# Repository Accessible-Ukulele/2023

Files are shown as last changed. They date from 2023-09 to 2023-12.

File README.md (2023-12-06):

# Accessible Ukulele
A repository for project code, reports, and more. NOT FINAL   
Created by:  
Kaleb Keller,   
Ryan Loar,  
Kameron Lund,  
and Dominic Pedavoli  

The Accessible Ukulele strives to eliminate the fine motor skills required to play the ukulele, to make playing music more accessible for amputees or those with fine motor control disabilities. The device allows the user to play chords at the press of a button using six precisely placed solenoids, that press down the strings of the ukulele.

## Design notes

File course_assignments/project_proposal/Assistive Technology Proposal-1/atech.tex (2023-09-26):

% This is the atech.tex This is where your writ ting will actually occur. In addition you will use this to display pictures, make tables, and format your paper. You should ONLY change things in this document.

% Calls up multiple packages that tell the computer ow you want to format the text and what neat tools you want to include so that you can use.

\documentclass[12pt]{article}
\usepackage{fancyhdr}
\usepackage{lettrine}
\usepackage[english]{babel}
\usepackage{graphicx}
\usepackage{gensymb}
\usepackage{listings}
\usepackage{multicol}
\usepackage{amsmath}
\usepackage{fancyvrb}
\usepackage{verbatim}
\usepackage{float}
\usepackage{multirow}
\usepackage{mathdesign}
\usepackage{txfonts}
\usepackage{mathrsfs}
\usepackage[justification=centering]{caption}
\usepackage{subcaption}
\usepackage{mdsymbol}
\usepackage{wrapfig}
\makeatletter
\def\mycatheader#1{\multicolumn{\tabu@nbcols}{c}{#1}}
\makeatother
\pagestyle{fancy}
\usepackage{mcode}
\providecommand{\e}[1]{\ensuremath{\times 10^{#1}}}

% Your class and semester here!
\lfoot{ECEN 1400}
\rfoot{Fall 2023}
 
% Defines that all Images are in the folder "images/" so that we don't have to type it repeatedly
\graphicspath{ {images/} }

% Catchy Name of your Project followed by 
\title{Atech Proposal: your project name}
%  followed by 
% Names {First Last} in Alphabetical Order by Last Name Go in Here 
\author{
  Name One \footnote{email1},
  Name Two \footnote{email2},
  Name Three \footnote{email3},
  Name Four \footnote{email4}\\
    {\normalsize 
   Lecture Section 100, ECEN 1400}\\
 }

% Tells the Document you are ready to start typing
\begin{document}

% Explains to the document to put in the Title, Names  onto a cover page
\maketitle

% This should be an ~200 word summary of the proposal
\begin{abstract}
An abstract is a block of text at the beginning of the paper that is usually around 200 words long. It is a conclusive statement of your entire proposal. 
\end{abstract}

% This ends the Title and Abstract page and lets you move on to the real report!

%This makes a new page 
\newpage

% This will make a Table of contents that Updates Automatically!
\tableofcontents

% This ensures it stays on its own page -- please be sure to do a new page before each new section (not subsection)
\newpage

% Begin a New Overarching topic
\section{Inspiration}
\newpage

\section{Project Scope}
The \textbf{scope} of the project will help you define the effort required and your plan to meet the specifications. This will help you figure out if the project is \textit{right sized} for the time you have. This judgement will depend on your skills - one size does not fit all.
% Begin a Sub-Topic
\subsection{Goals}
The goal and mission of your group should be in here. In addition pertinent information regarding your client (if you have one) will be very important. You should be explaining who they are before you explain what they need you to do! Be \textbf{very} descriptive.  What are your goals for the project? What is important for you to get out of it? These could be learning goals or specific performance milestones. (not the dates of PDR, CDR etc but what will be done) 

\subsection{Team Assignments}
Each should include a short description of what each person will do, sufficient to judge the effort and complexity of their task. What background, if any, does the team member bring that is relevant to achieving their goal? Everyone must do some technical design work – not just paperwork. Though certain students may have a larger or smaller technical role.

\subsection{Plans to Achieve Goal}
Depending on the project, describe:
\begin{itemize}

\item What will you design and build vs. what will you buy? (Buying pieces to help the design work is acceptable for this project)

\item What resources are available (people, existing designs) that increase your capability?

\item What will your project NOT do?

\end{itemize}

\newpage

\section{Specifications}

To the best of your ability now, list quantifiable performance specifications. Be as complete as you can. It is much more important that you think of the entry, (e.g. “Battery Life in Hours”) than you know the value.

% have text introducing the table

\begin{itemize}

    \item Start with categories, then work on individual entries.

    \item Present this in the form of a table. For each spec, list minimum, nominal and maximum values if known, \textit{as appropriate}. Include a column for units.

\end{itemize}
%Google "latex table format" 

\newpage

\section{Design Iteration}

% Sub-Topic 1
\subsection{Design Elements}
% each as appropriate for your project
This should be a full length description of your initial ideas/parts with beautiful pictures to match. I have elected to leave in a groups photo of their project to show how to insert a graphic below!

% This is how you insert a graphic. This is very, very important. Have this ready to go at all points. Always caption and use a label with your figure. Always reference the figure before you insert it.

% How to call a figure that has been labeled so you don't have to keep track of numbers.

Figure \ref{fig:frame} shows a rendering of our project frame including (be descriptive) a clear object in the front and the mounting system.

\begin{figure}[H]
% Puts your image in the center of the page, multiple other justifications are able to be done
\centering
    % Actually include the graphic
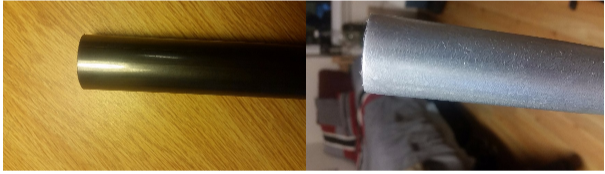
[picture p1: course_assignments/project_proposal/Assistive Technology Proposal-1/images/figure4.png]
    
    % CAPTIONS ARE VERY IMPORTANT NO FLOATING PICTURES
    \caption{Comparison of galvanized metal (right) to weldable steel (left)}
    % This is how we can tell the code what picture we are referencing.
    \label{fig:frame}
\end{figure}

\begin{itemize}
\item Block Diagram Electrical
\item Software Flow Chart
\item Block Diagram Mechanical
\item Sketch of package / external design - hand drawings are acceptable (if done in dark ink and readable - but preliminary CAD is encouraged. This should include how major components (in size or importance) are expected to “fit” in the project.
\item \textbf{Estimated}  bill of materials (BOM) as a \textbf{table} including cost for critical and expensive items. Total the cost. 
\end{itemize}

% Please use numbers/equations

In case you were wondering, you can use equations! See Equation \ref{eq:Strain}. This one happens to represent strain on a bar.

% This is how to use an equation, a mathematical Symbol, Fractions, and underscores
\begin{equation}
    \sigma = \frac{F}{A_{0}}
    \label{eq:Strain}
\end{equation}

% New Topic
\newpage
\section{Risk Mitigations}
\begin{itemize}
    \item List possible (significant) risks to success and briefly describe your plan to overcome these. Suggest minimal performance and alternative approaches or alternative goals to be successful. (think safety, supply chain issues, illness of team member, etc..)
    \item Think creatively about this.
\end{itemize}

% Another Figure example
In Figure \ref{fig:cage} you can see an old picture of the cage. 
\begin{figure}[H]
\centering
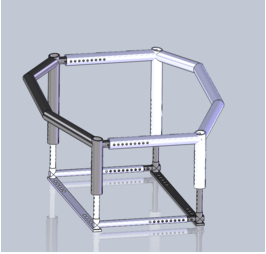
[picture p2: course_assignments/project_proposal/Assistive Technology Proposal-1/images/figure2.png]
    
    \caption{Original 3D model of the cage}
    \label{fig:cage}
\end{figure}

\newpage
\section{Timeline}
% New Sub-Topic
Look at the semester schedule including assignment milestones. Create a list of performance milestones by date. (what will get done by when) Include deliverables on sub-tasks such as electronics or software.  Use a \textbf{Gantt Chart} made using excel or something like excel.  Avoid using commercial packages or templates to create the chart, especially those that are complicated.

\newpage
\section{Tools}
Tools that will be used (laser cutter, 3D printer, sewing machines, milling machine). 
Put in any other tools you might have used!

\newpage
\section{Anything else you can think of that is helpful}

\newpage
\section{Closing Statements}
A strong argument for the success of this project
 
\newpage

% Anything Pertinent but without a real place, or if it doesn't fit in your discussion section.
\section{Appendix}

% Close and render the paper to a PDF format
\end{document}

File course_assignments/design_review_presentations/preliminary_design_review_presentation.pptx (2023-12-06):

## The Accessible Ukulele The Joule Jugglers

Dominic Pedavoli
Kaleb Keller
Kameron Lund
Ryan Loar

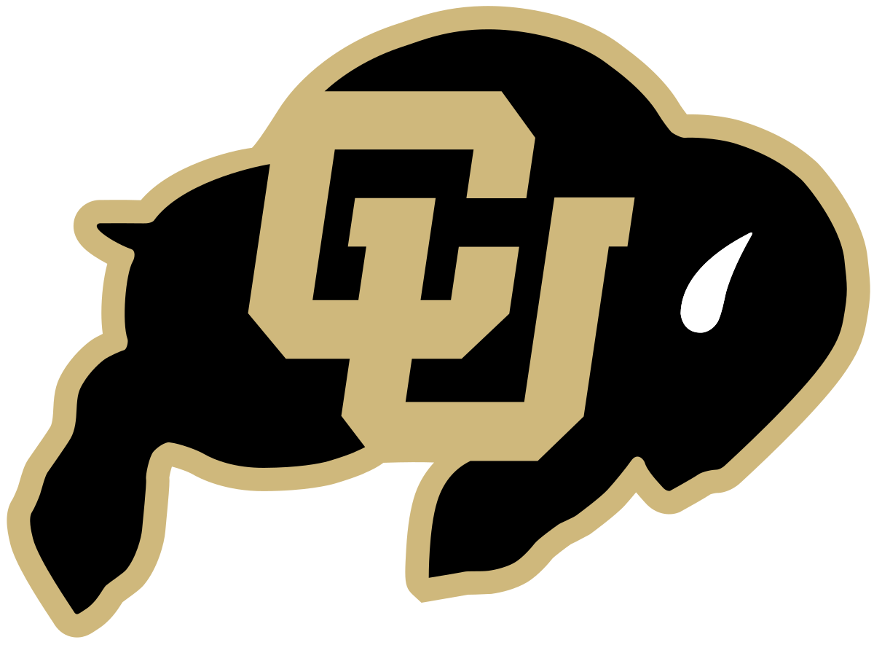
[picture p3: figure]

## For The Love of Music

- Form of expression
- Relaxing
- Outlet to relieve stress
- Not always accessible to everyone

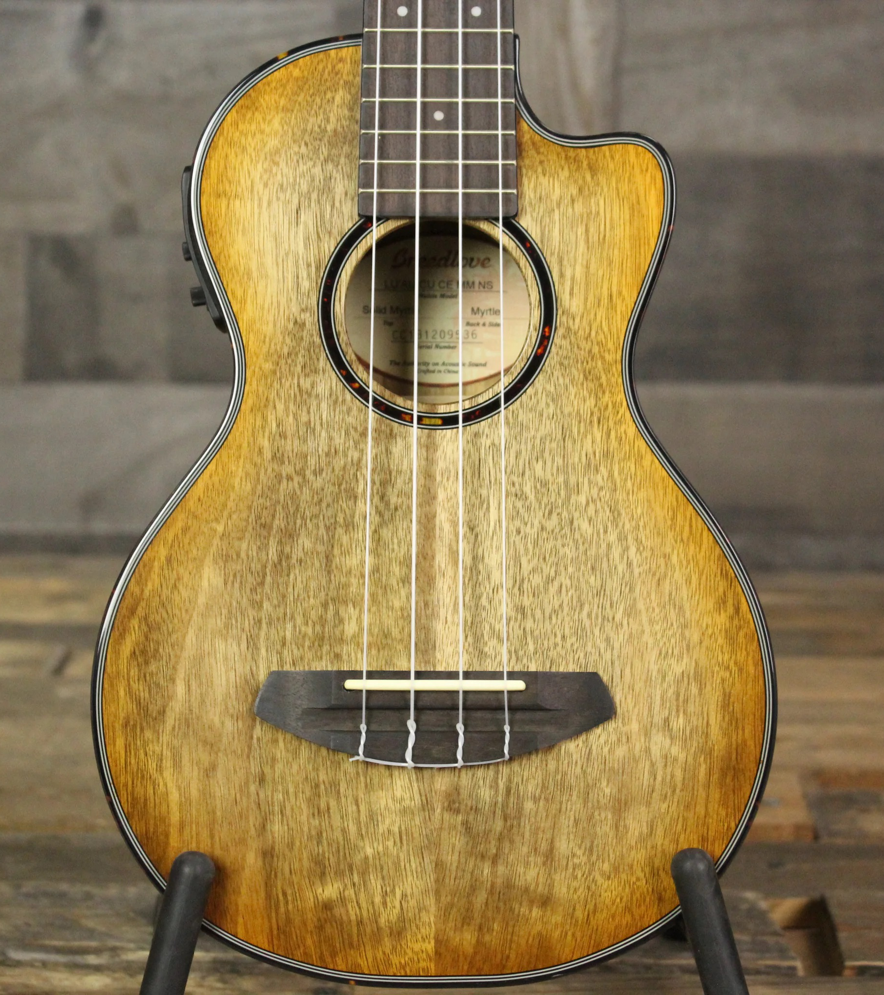
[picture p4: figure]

## Problem Statement

The ability to play music is not accessible to everyone. Those with a fine motor control disability can find it difficult to play music as an outlet of expression. This problem can begin to be solved by simplifying the way instruments can be played.

## Outline

Our Target Market

Design Inspiration

Expected Timeline

Cost of Materials

Original Circuit Diagrams

Plans for Testing

Goals

Definition of Success

## Client Introduction – Our Target Market

Intended for those who lack fine motor control in hands
Not trying to replace the ukulele
Simplifying the way, it's played and giving options to those in need

## Design Inspiration

- Guitar Hero (Top Right)
- Beginner Chord (Top Left)
- EZ Fret (Bottom Left)
- Our Initial Design Idea (Bottom Left)

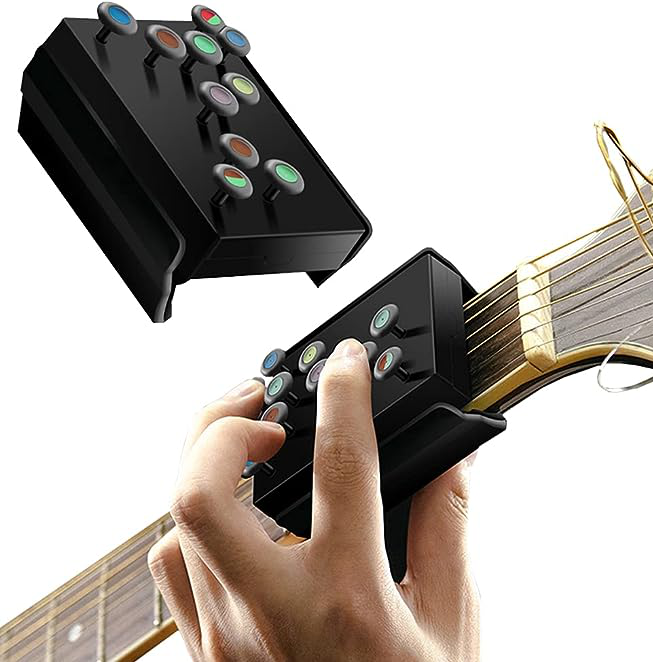
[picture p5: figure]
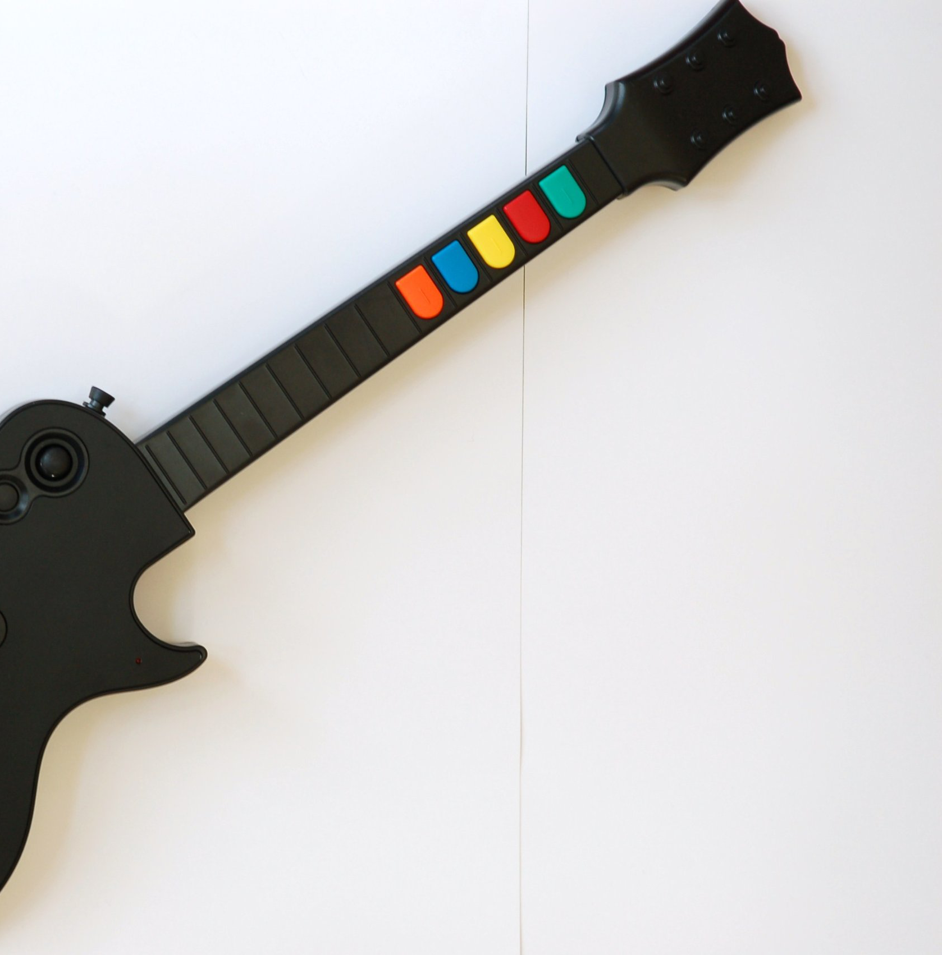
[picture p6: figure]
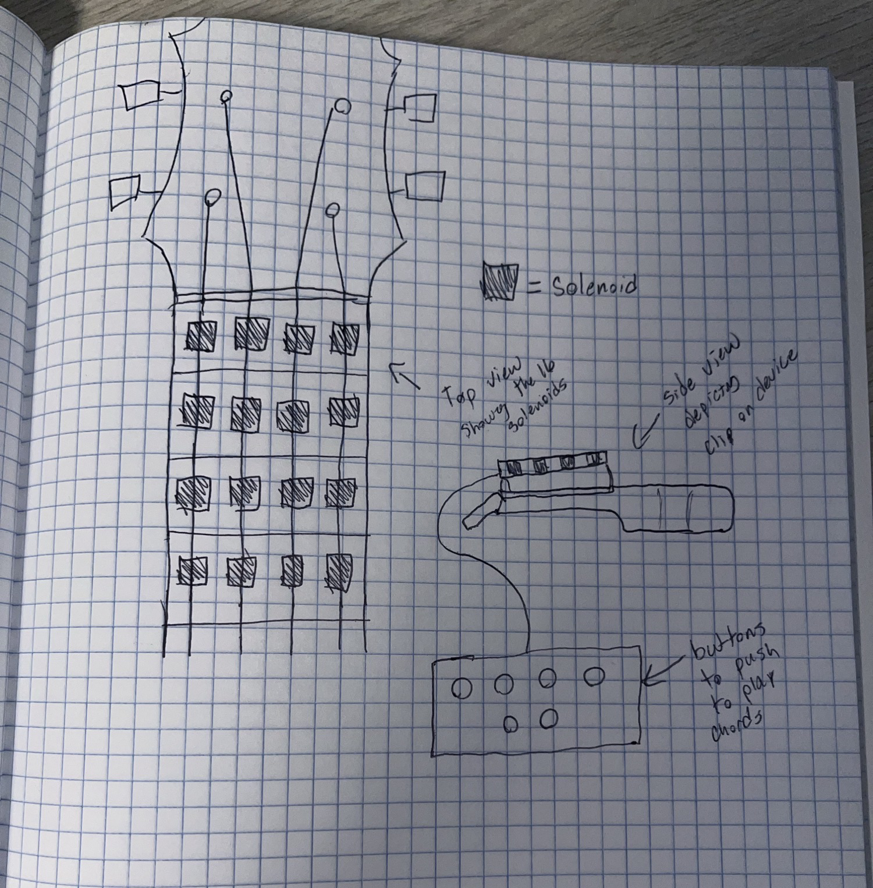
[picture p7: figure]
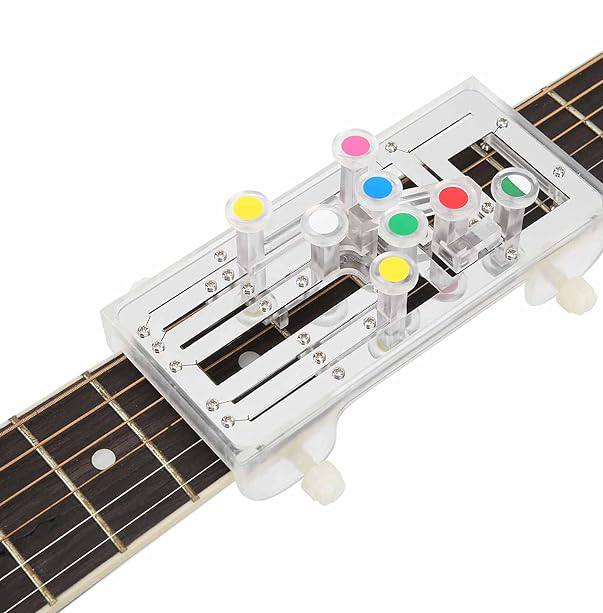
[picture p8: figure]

## Timeline/Task Assignments

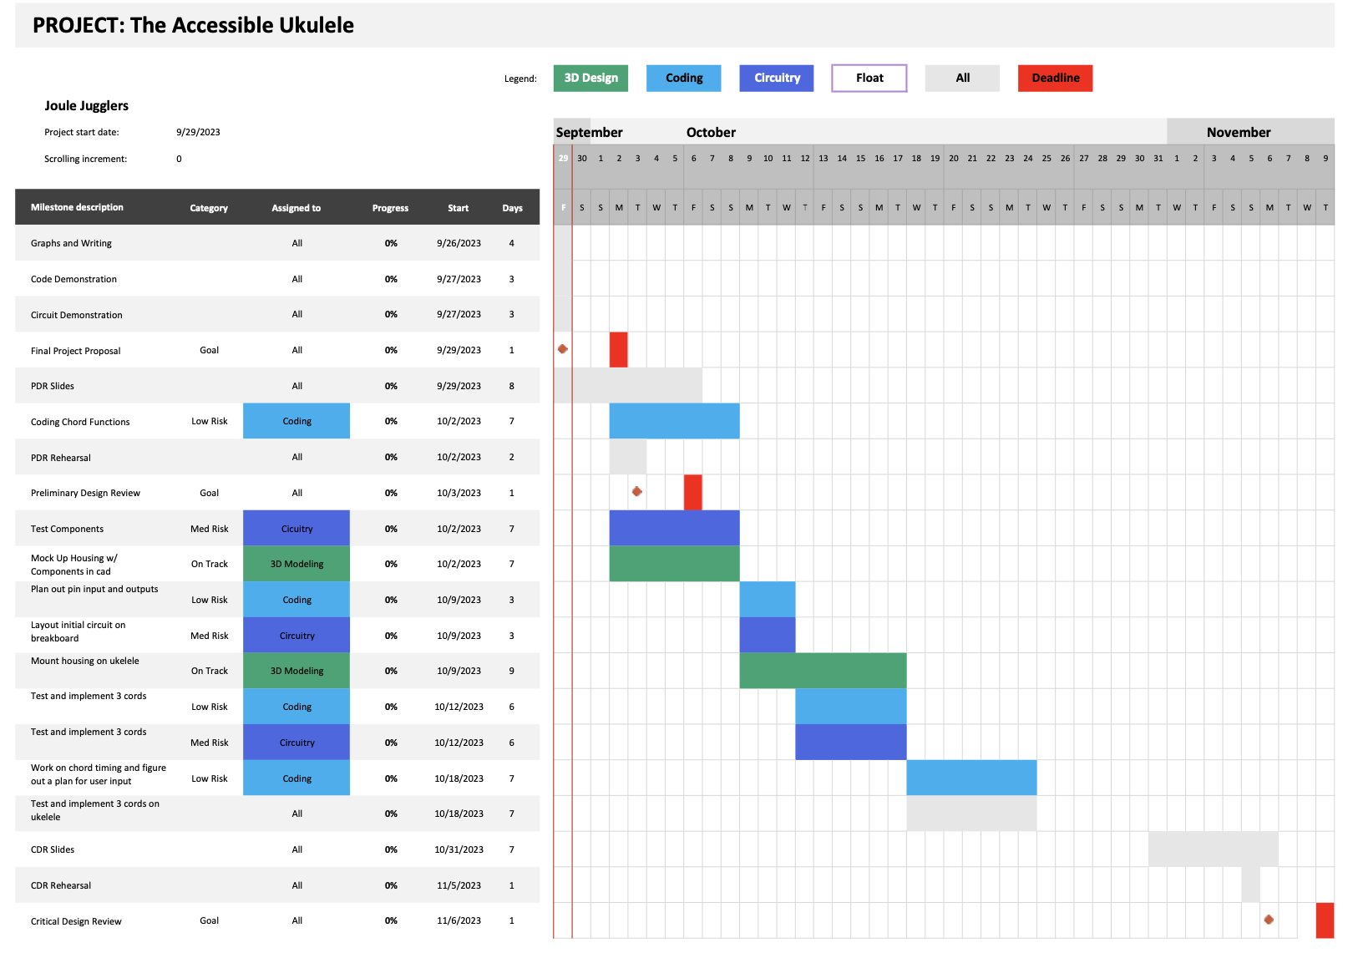
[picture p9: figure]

Gantt chart of our timeline

- Kameron - coding
- Dominic - circuitry
- Kaleb - 3D design
- Ryan - float
- Organizing time based on musical milestone
- Design as individuals and come back together to test and iterate as a group

## Budget/Bill of Materials

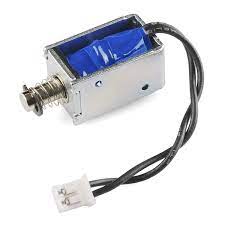
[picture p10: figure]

Solenoids (x16):
Buttons (x4):
Arduino Mega (Elegoo) (x1):
Transistors (x16)
Miscellaneous:
Total:
Budget Maximum:
Margin:

$88.00
$51.80
$21.00
$0.00
$15.00
$175.80
$300.00
$124.20

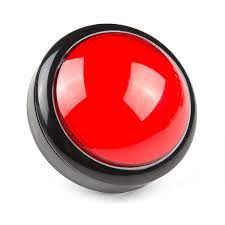
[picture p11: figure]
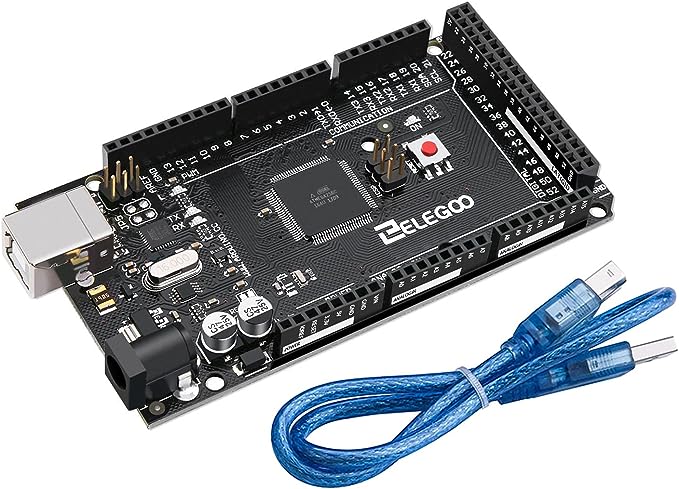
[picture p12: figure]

## Plans for Testing

- Test materials immediately after their arrival
- Test code consistently and thoroughly as we develop it
- Test circuits on breadboard before soldering wires
- Print housing and parts early
- Test compilation of parts
- Regularly test all tasks together once completed

## Circuit Diagram

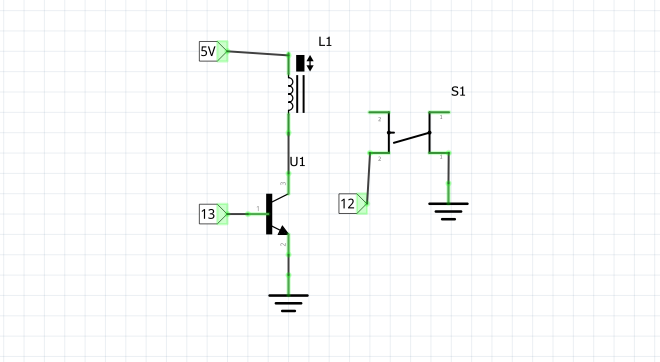
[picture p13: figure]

*Diagram for 1 of 16 solenoids

## Definition of Success

With this project we will…
- Respect and preserve the individual creativity of the musician
- Fundamentally change the range of physical motion required for musical expression
- Respect the instrument for its complexity (it's not a toy)
- Design in a way that maximizes accessibility while minimizing triviality
- Separate music as an art form from physical ability

## Conclusion

- Ease the process of playing stringed instruments
- Keep outcomes (sound) the same
- Regularly test (physical and digital)
- Explore new input avenues (buttons vs motion control vs app)
- Explore coding solutions to physical problems (manage button switching)

## Any Questions?

## How Do Solenoids Work?

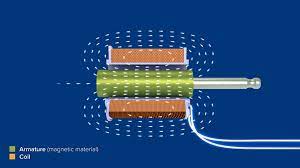
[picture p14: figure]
A diagram of a device
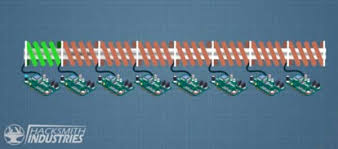
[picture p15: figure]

## What If The Solenoids Don't Work?

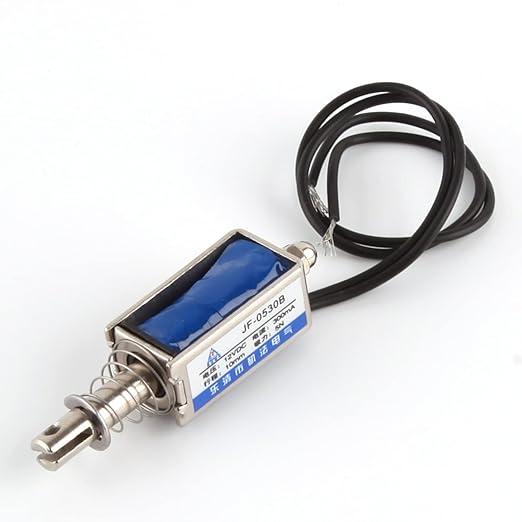
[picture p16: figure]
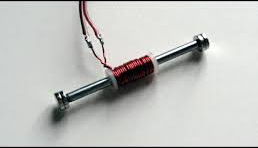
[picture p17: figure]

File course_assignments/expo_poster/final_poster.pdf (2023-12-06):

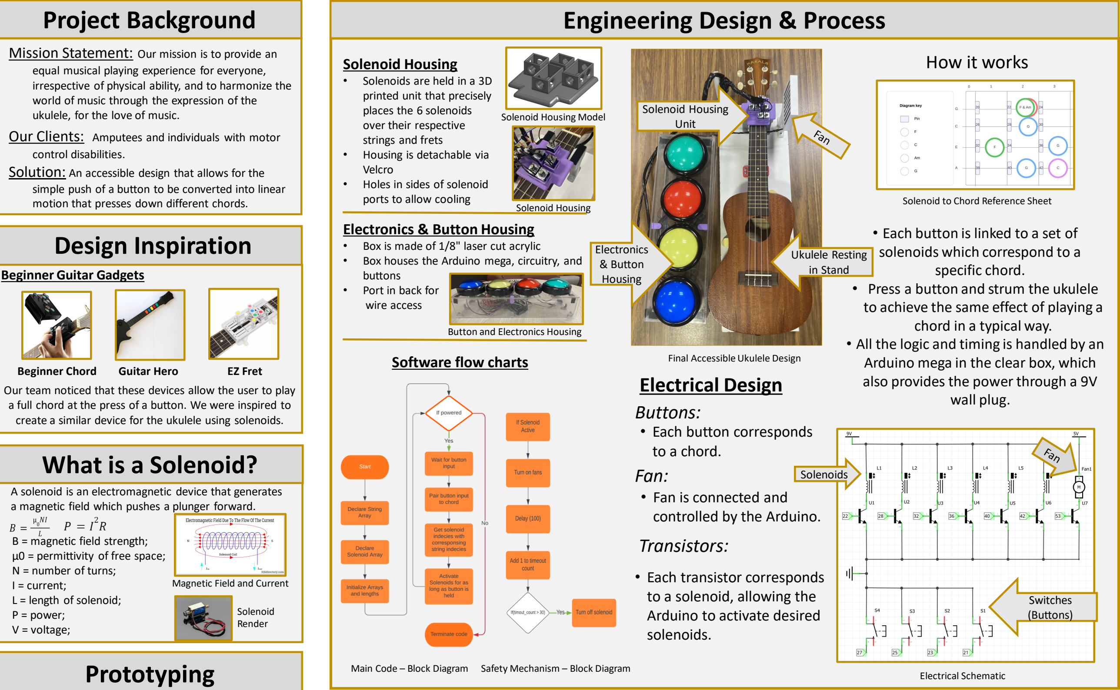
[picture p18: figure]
ukulele, for the love of music.; control disabilities.; Project Background; Prototyping; Engineering Design & Process; Beginner Guitar Gadgets; Software flow charts; • Each button corresponds to a chord.; Buttons:; Electrical Schematic; What is a Solenoid?; Main Code – Block Diagram; Safety Mechanism – Block Diagram; Beginner Chord; Solenoid Housing; • Solenoids are held in a 3D printed unit that precisely places the 6 solenoids over their respective strings and frets • Housing is detachable via Velcro • Holes in sides of solenoid ports to allow cooling; How it works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

Mission Statement: Our mission is to provide an equal musical playing experience for everyone, irrespective of physical ability, and to harmonize the world of music through the expression of the

Our Clients: Amputees and individuals with motor

Solution: An accessible design that allows for the simple push of a button to be converted into linear motion that presses down different chords.

A solenoid is an electromagnetic device that generates a magnetic field which pushes a plunger forward.

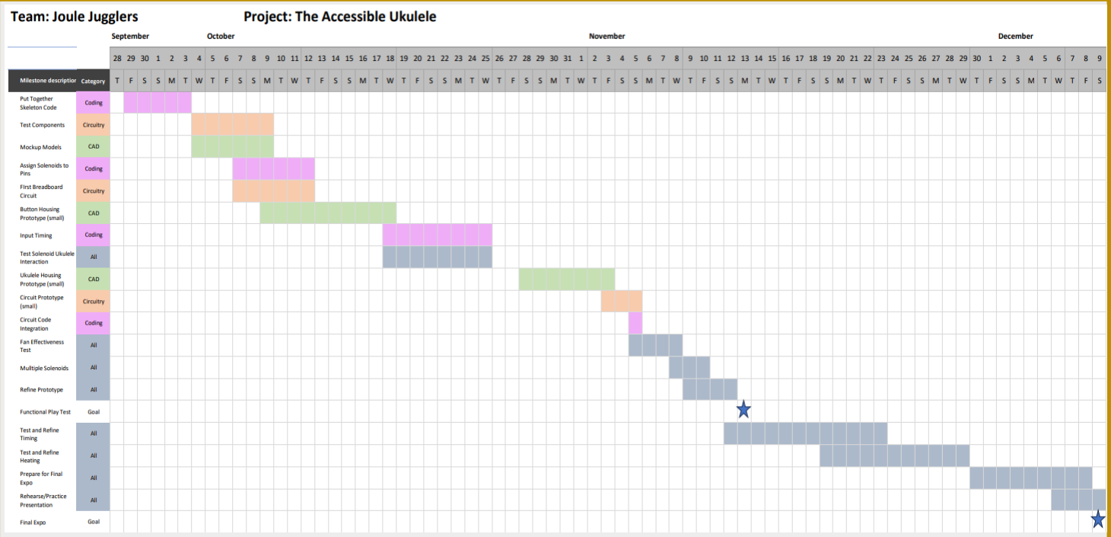
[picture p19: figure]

### - Potential exposure to live wires (as few as possible

with our constraints).

### - Solenoids are prone to producing a large amount of

heat.

### - Fan engages when the solenoid(s) are active, ensuring

that the solenoid never reaches above 100° F.

### - Fans use convection cooling to push air past the

solenoid housing, dispersing the heat.

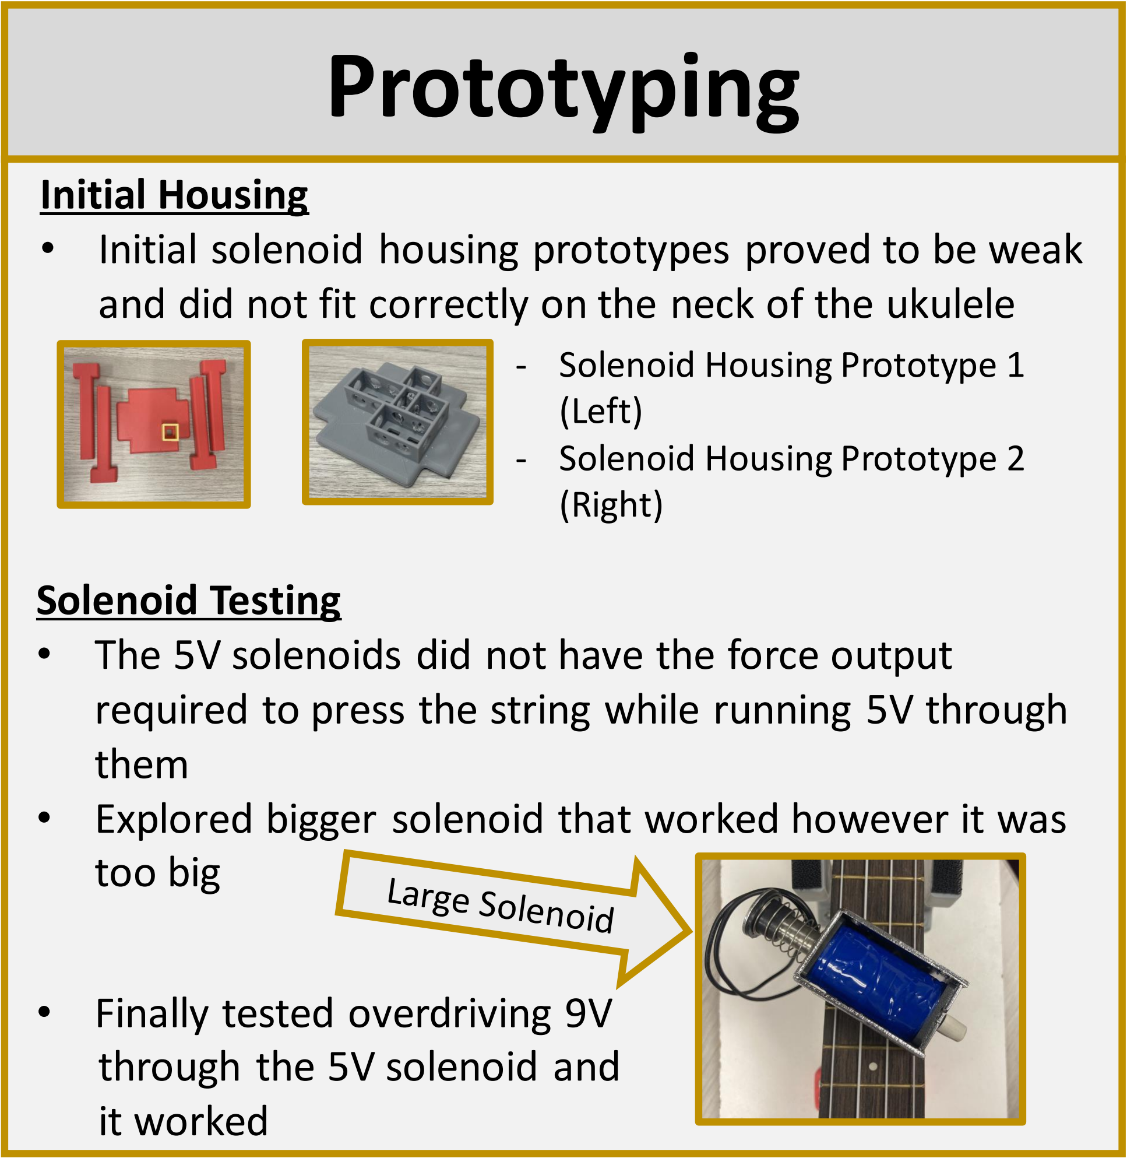
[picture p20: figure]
Initial Housing; Solenoid Testing; them; too big; • Finally tested overdriving 9V through the 5V solenoid and it worked; - Solenoid Housing Prototype 1 (Left) - Solenoid Housing Prototype 2 (Right)

- Initial solenoid housing prototypes proved to be weak and did not fit correctly on the neck of the ukulele
- The 5V solenoids did not have the force output required to press the string while running 5V through
- Explored bigger solenoid that worked however it was

# Heat Dissipation

Our team noticed that these devices allow the user to play a full chord at the press of a button. We were inspired to create a similar device for the ukulele using solenoids.

# Testing

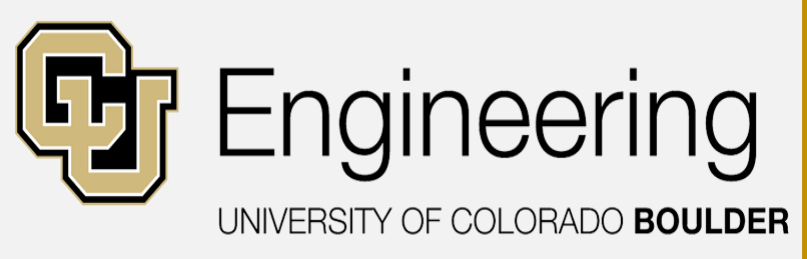
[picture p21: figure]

# Joule Jugglers: Kaleb Keller, Ryan Loar, Kameron Lund, and Dominic Pedavoli

## Piket-May - ECEN1400 Section 100 First Year Engineering Projects – Fall 2023

# Accessible Ukulele

- Box houses the Arduino mega, circuitry, and

# Safety Concerns

Seconds Activated | Temperature °F (No Fan) | Temperature °F (With Fan)
- Our main concern was with the heat of the solenoids 0 • Below is the data we gathered on the effect of | 72.34 | 74.71
22.5 fan cooling | 75.55 | 79.99
45 | 87.02 | 85.26
67.5 | 95.22 | 89.66
90 | 103.70 | 93.17
- Our main concern was with the heat of the solenoids.

### - Below is the data we gathered (three trials) on the effect

of fan cooling on the surface temperature of solenoids.

### - All the logic and timing is handled by an

Dimensions
- Overall
Footprint: 10
" X 26"
- Height: 7"

# Housing

Technical Development: All Members learned CAD,
Laser Machining, Soldering, and 3D design to help put the project together and ensure its success.

Team Development: Each member came forward and displayed one or more of their strengths/talents to help complete what needed to get done on time while making sure their work is up to standard.

# Lessons Learned

# Future Developments

-Implement additional solenoids allowing the user to play more chords

-Finding alternative solenoids that are similar in size, yet output the minimum force required without being overdriven

# Budget

Quantity & Product | Price Per Item | Total Cost
6 5V Solenoids | $5.50 each | $33.00
6 13.2 x 12.1 mm Copper Heatsinks | $1.95 each | $11.70
6 Transistors | $0.00 each | $0.00
4 Buttons | $12.95 each | $51.80
1 Arduino Mega (ELEGOO) | $21.00 each | $21.00
1 30 x 30 mm fan | $3.50 each | $3.50
1 9V DC Power Supply | $14.00 each | $14.00
Total | - | $135.00
Margin | - | $165.00

# Gantt Chart

Professor Melinda Piket-May, Tim May, Jonah Spicher, and Rylee Beach.

# Acknowledgements

Surface Temperature Data

Complete Housing CAD Model

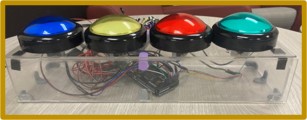
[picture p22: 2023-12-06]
resources/project_photos_videos/electronics_housing.jpg

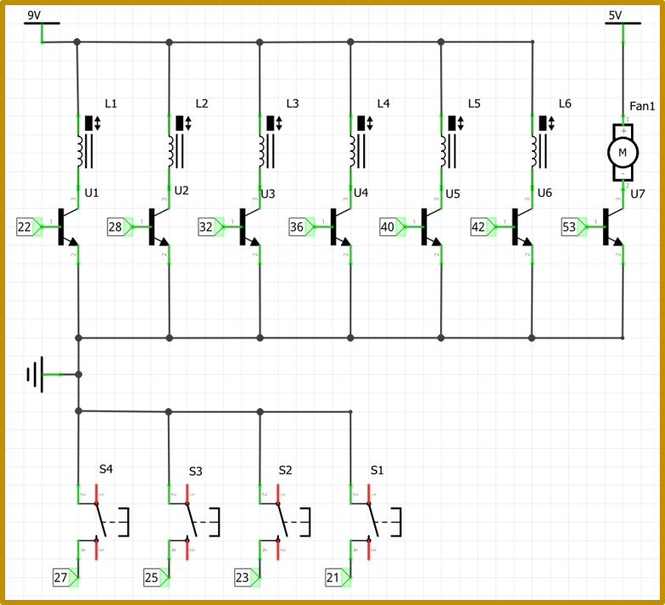
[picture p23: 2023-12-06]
resources/electronics_schematic.png

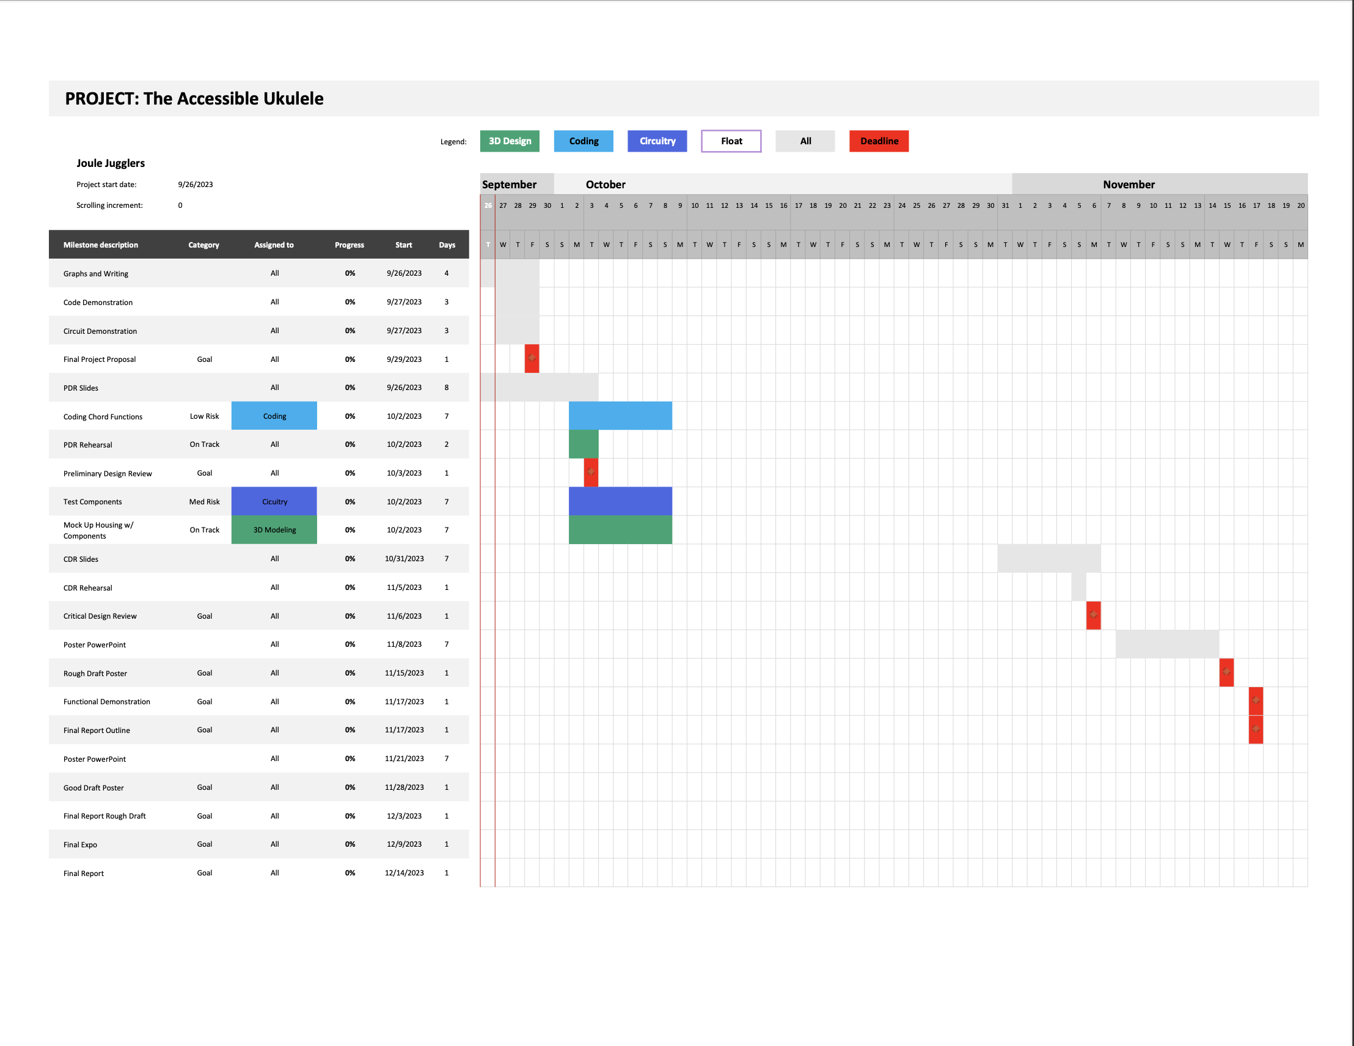
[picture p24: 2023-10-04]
course_assignments/project_proposal/ECEN1400_FinalProjectProposal_ganttChart.png

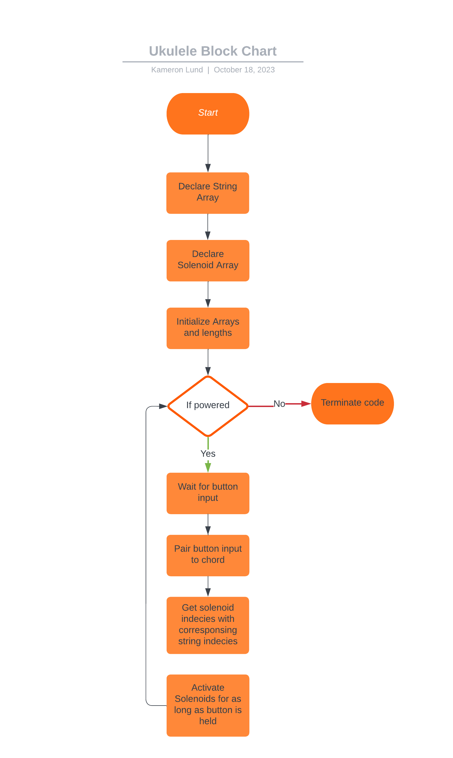
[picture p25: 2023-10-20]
resources/Ukulele Block Chart.png

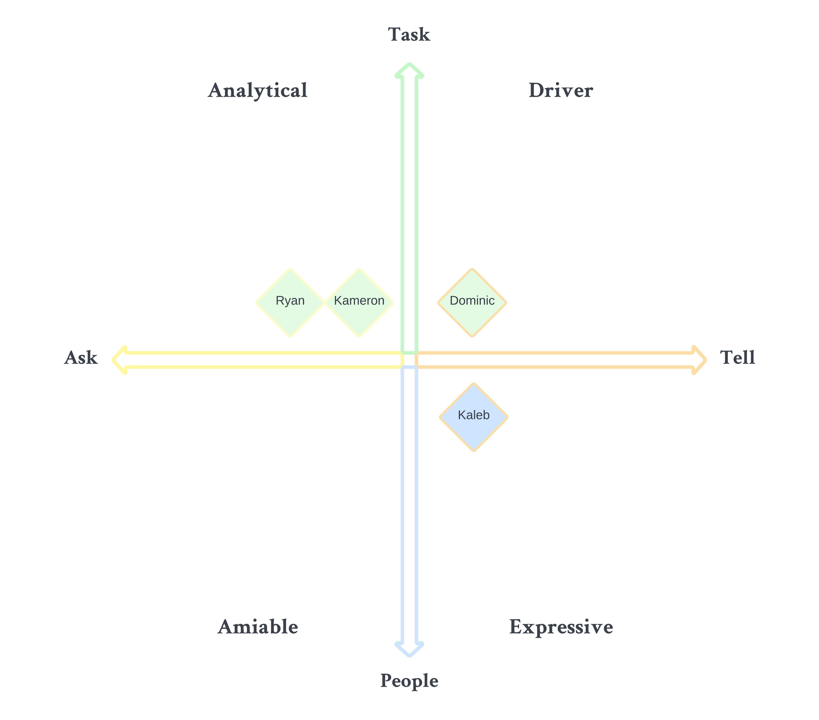
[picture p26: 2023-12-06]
resources/social_styles_grid.jpeg

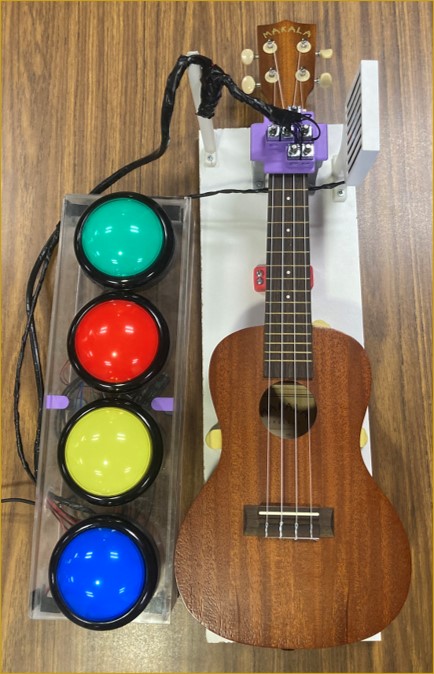
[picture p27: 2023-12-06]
resources/project_photos_videos/final_product.jpg

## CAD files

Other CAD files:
cad_models/accessible_ukulele.x_t
cad_models/electronics_housing.x_t
cad_models/fan_cage_sides.x_t
cad_models/fan_cage_top.x_t
cad_models/housing_supports.x_t
cad_models/solenoid_fan_cage.x_t
cad_models/solenoid_fan_stand.x_t
cad_models/solenoid_housing_legs.x_t
cad_models/solenoid_housing_platform.x_t
cad_models/solenoid_presser.x_t
cad_models/ukulele_body_holds.x_t
cad_models/ukulele_neck_holds.x_t
cad_models/ukulele_wood_platform.x_t
cad_models/wire_holder.x_t

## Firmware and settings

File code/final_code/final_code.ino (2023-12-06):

void setup() 
{
    //pin declarations
    const int GREEN = 23;
    const int RED = 25;
    const int YELLOW = 27;
    const int BLUE = 29;
    const int FAN = 7;

    //RED button
    pinMode(RED, INPUT_PULLUP);
    //BLUE button
    pinMode(GREEN, INPUT_PULLUP);
    //YELLOW button
    pinMode(YELLOW, INPUT_PULLUP);
    //BLUE button
    pinMode(BLUE, INPUT_PULLUP);

    //FAN pin
    pinMode(FAN, OUTPUT);

    //solenoid pins
    pinMode(22, OUTPUT);
    pinMode(28, OUTPUT);
    pinMode(32, OUTPUT);
    pinMode(36, OUTPUT);
    pinMode(40, OUTPUT);
    pinMode(42, OUTPUT);
}

void loop() 
{
    //c chord
    if (digitalRead(GREEN) == HIGH)
    {
        digitalWrite(42, HIGH);
        digitalWrite(40, LOW);
        digitalWrite(36, LOW);
        digitalWrite(32, LOW);
        digitalWrite(28, LOW);
        digitalWrite(22, LOW);

        digitalWrite(FAN, HIGH);

    }
    //g chord
    else if (digitalRead(RED) == HIGH)
    {
        digitalWrite(42, LOW);
        digitalWrite(40, HIGH);
        digitalWrite(36, HIGH);
        digitalWrite(32, LOW);
        digitalWrite(28, HIGH);
        digitalWrite(22, LOW);

        digitalWrite(FAN, HIGH);
    }
    //a chord
    else if (digitalRead(YELLOW) == HIGH)
    {
        digitalWrite(42, LOW);
        digitalWrite(40, LOW);
        digitalWrite(36, LOW);
        digitalWrite(32, LOW);
        digitalWrite(28, LOW);
        digitalWrite(22, HIGH);

        digitalWrite(FAN, HIGH);
    }
    //f chord
    else if (digitalRead(BLUE) == HIGH)
    {
        digitalWrite(42, LOW);
        digitalWrite(40, LOW);
        digitalWrite(36, LOW);
        digitalWrite(32, HIGH);
        digitalWrite(28, LOW);
        digitalWrite(22, HIGH);

        digitalWrite(FAN, HIGH);
    }


    else
    {
        digitalWrite(42, LOW);
        digitalWrite(40, LOW);
        digitalWrite(36, LOW);
        digitalWrite(32, LOW);
        digitalWrite(28, LOW);
        digitalWrite(22, LOW);

        digitalWrite(FAN, LOW);
    }
}

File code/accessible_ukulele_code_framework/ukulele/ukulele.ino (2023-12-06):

//global variables
const int stringArrayLength = 12;
char* string_frets[stringArrayLength];
int solenoid_pins[stringArrayLength];
int button[4] = {29, 23, 25, 27};
char string_fret[2] = {'z', 'z'};
char active_note = '!';
int solenoid_index;
int button_hold_start;
int time_button_held;
int pressed_button = 4;

void setup()
{
    //setup serial console
    Serial.begin(9600);

    //red green blue yellow
    setupStringArrays();

    pinMode(button[0], INPUT_PULLUP);
    pinMode(button[1], INPUT_PULLUP);
    pinMode(button[2], INPUT_PULLUP);
    pinMode(button[3], INPUT_PULLUP);

    for(int i = 0; i < sizeof(solenoid_pins); i++)
    {
        pinMode(solenoid_pins[i], OUTPUT);
    }
}

void loop()
{
    switch(pressed_button)
    {
        //held for too long
        case -1:
            clearActiveNote();
            analogWrite(36, 0);
            delay(1000);
        //c
        case 0:
            playC();
            break;
        //a
        case 1:
            playA();
            break;
        //f
        case 2:
            playF()
            analogWrite(36, 255);
            break;
        //g
        case 3:
            playG();
            break;
        case 4:
            analogWrite(36, 0);
            break;

    }
    pressed_button = buttonCheck();

    if(time_button_held >= 1500)
    {
        pressed_button = -1; 
        loop();
    }
}

//check on if any buttons are being pressed
int buttonCheck() 
{
    //red - c
    if (digitalRead(button[0]) == HIGH) 
    {
        time_button_held = millis() - button_hold_start;
        Serial.println("Hello, red");
        return 0;
    } 

    //green - a
    else if (digitalRead(button[1]) == HIGH) 
    {
        time_button_held = millis() - button_hold_start;
        Serial.println("Hello, green");
        return 1;
    } 

    //blue - f
    else if (digitalRead(button[2]) == HIGH) 
    {
        time_button_held = millis() - button_hold_start;
        Serial.println("Hello, blue");
        return 2;
    } 

    //yellow - g
    else if (digitalRead(button[3]) == HIGH) 
    {
        time_button_held = millis() - button_hold_start;
        Serial.println("Hello, yellow");
        return 3;
    } 

    //none
    else 
    {
        Serial.println("Hello, none");
        button_hold_start = millis();
        return 4;
    }
}

//track down which index is attached to the solenoid that we want
//returns an index when given a string_fret combination to find
//returns index or returns -1 on fail
int findSolenoidIndex(char string_fret[2])
{
    //if we use char* we will have to manually write .find
    for(int i = 0; i < sizeof(string_frets); i++)
    {
        if(string_frets[i][0] == string_fret[0] && string_frets[i][1] == string_fret[1])
        {
            return i;
        }
    }
    return -1;
}

//option 1
//ex function yet to be implemented
//solenoid indicies size, for loop fol0ing, that calls to find each string and activated respective solenoids
void playNote(int solenoid_indicies[], int solenoid_indicies_size)
{

}

//option 2
//ex function yet to be implemented

//c a f g

void playC()
{
    string_fret[0] = 'A';
    string_fret[1] = 3;
    solenoid_index = findSolenoidIndex(string_fret);
    if (solenoid_index == -1) {}//error
    analogWrite(solenoid_pins[solenoid_index], 255);

    active_note = 'C';
}
void releaseC()
{
    string_fret[0] = 'A';
    string_fret[1] = 3;
    solenoid_index = findSolenoidIndex(string_fret);
    if (solenoid_index == -1) {}//error
    analogWrite(solenoid_pins[solenoid_index], 0);

    active_note = '!';
}

//a minor
void playA()
{
    string_fret[0] = 'G';
    string_fret[1] = 2;
    solenoid_index = findSolenoidIndex(string_fret);
    if (solenoid_index == -1) {}//error
    analogWrite(solenoid_pins[solenoid_index], 255);

    // string_fret = {'C', 1};
    // solenoid_index = findSolenoidIndex(string_fret);
    // if (solenoid_index == -1) {}//error
    // analogWrite(solenoid_pins[solenoid_index], 255);

    active_note = 'A';
}
void releaseA()
{
    string_fret[0] = 'G';
    string_fret[1] = 2;
    solenoid_index = findSolenoidIndex(string_fret);
    if (solenoid_index == -1) {}//error
    analogWrite(solenoid_pins[solenoid_index], 0);

    // string_fret = {'C', 1};
    // solenoid_index = findSolenoidIndex(string_fret);
    // if (solenoid_index == -1) {}//error
    // analogWrite(solenoid_pins[solenoid_index], 0);

    active_note = '!';
}

void playF()
{
    string_fret[0] = 'E';
    string_fret[1] = 1;
    solenoid_index = findSolenoidIndex(string_fret);
    if (solenoid_index == -1) {}//error
    analogWrite(solenoid_pins[solenoid_index], 255);

    string_fret[0] = 'G';
    string_fret[1] = 2;
    solenoid_index = findSolenoidIndex(string_fret);
    if (solenoid_index == -1) {}//error
    analogWrite(solenoid_pins[solenoid_index], 255);

    active_note = 'F';
}
void releaseF()
{
    string_fret[0] = 'E';
    string_fret[1] = 1;
    solenoid_index = findSolenoidIndex(string_fret);
    if (solenoid_index == -1) {}//error
    analogWrite(solenoid_pins[solenoid_index], 0);

    string_fret[0] = 'G';
    string_fret[1] = 2;
    solenoid_index = findSolenoidIndex(string_fret);
    if (solenoid_index == -1) {}//error
    analogWrite(solenoid_pins[solenoid_index], 0);

    active_note = '!';
}

void playG()
{
    string_fret[0] = 'C';
    string_fret[1] = 2;
    solenoid_index = findSolenoidIndex(string_fret);
    if (solenoid_index == -1) {}//error
    analogWrite(solenoid_pins[solenoid_index], 255);

    string_fret[0] = 'E';
    string_fret[1] = 3;
    solenoid_index = findSolenoidIndex(string_fret);
    if (solenoid_index == -1) {}//error
    analogWrite(solenoid_pins[solenoid_index], 255);

    string_fret[0] = 'A';
    string_fret[1] = 2;
    solenoid_index = findSolenoidIndex(string_fret);
    if (solenoid_index == -1) {}//error
    analogWrite(solenoid_pins[solenoid_index], 255);

    active_note = 'G';
}
void releaseG()
{
    string_fret[0] = 'C';
    string_fret[1] = 2;
    solenoid_index = findSolenoidIndex(string_fret);
    if (solenoid_index == -1) {}//error
    analogWrite(solenoid_pins[solenoid_index], 0);

    string_fret[0] = 'E';
    string_fret[1] = 3;
    solenoid_index = findSolenoidIndex(string_fret);
    if (solenoid_index == -1) {}//error
    analogWrite(solenoid_pins[solenoid_index], 0);

    string_fret[0] = 'A';
    string_fret[1] = 2;
    solenoid_index = findSolenoidIndex(string_fret);
    if (solenoid_index == -1) {}//error
    analogWrite(solenoid_pins[solenoid_index], 0);

    active_note = '!';
}
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
